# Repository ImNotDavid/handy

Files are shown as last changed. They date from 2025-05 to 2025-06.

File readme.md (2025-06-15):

# HANDY

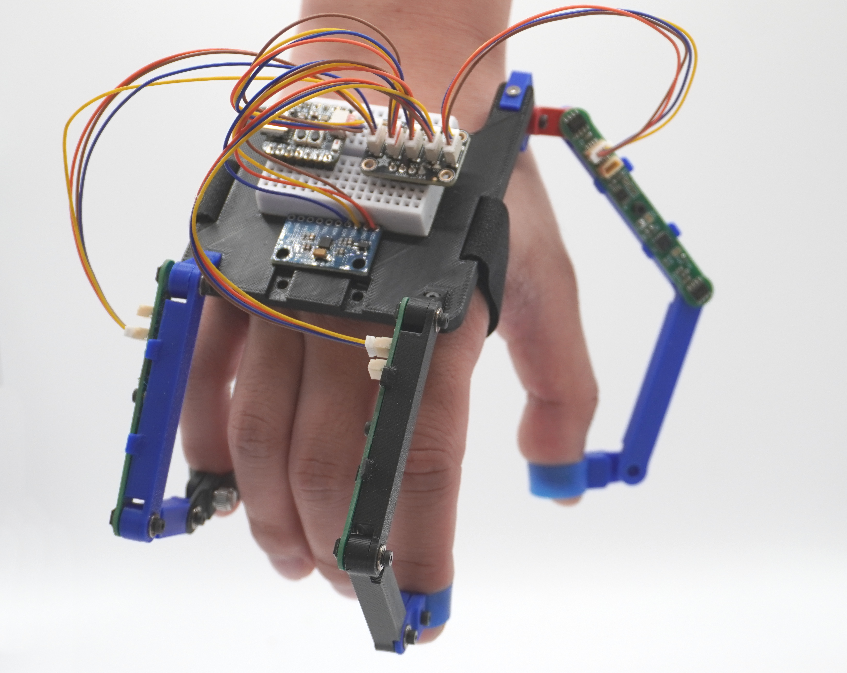
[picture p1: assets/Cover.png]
Handy cover image

## Overview
The Haptically-enabled and Afforable framework to control of Non-anthropomorphic robot manipulators for Data gatheringY (HANDY) is a very affordable data glove and ROS software stack to allow anyone to capture dexterous manipulation data.  

## Hardware 

The 3d model can be found at [this](https://cad.onshape.com/documents/4283529db481f6427532362c/w/a5ad88a1f793d7bc8f76de6a/e/f981b522771d813f689838bc) public onshape project. 

The lenghts of the linkages can be changed by editing variables in the `Passive Link` file or configuration values in `Main Assembly`. The size of the finger mounts can be edited similarly in `Finger Trap Net`. It is highly recommended to use [onshape-to-robot](https://github.com/Rhoban/onshape-to-robot) to convert the assembly into a URDF. The assembly, `URDF` has already been set up for this purpose and the config file [here](handy_ros2\urdf\config.json) has been configured to point to the correct file. You will need to change this to your own URL if you are making modifications. 
All parts can be printed in PLA at 0.16mm layer height. The following off the shelf components are required to assemble the Handy (5 fingered configuration):
- 10 of 6mm x 1mm diametrically magnetised magnet (found [here](https://www.first4magnets.com/product/6mm-dia-x-1mm-thick-diametrically-magnetised-n42-neodymium-magnet-20413)) 
- 20 of M2x3.2x2.5mm heat set insert with OD 
- 20 M2x6mm screws 
- 1 Mini Breadboard
- ESP32-S3 pyqt 

### PCB
All the gerber files for the PCB are found [here](pcb\output\handy_gbr.zip) and can be ordered from a manufacturer like JLCPCB for a low price. The component list is included in the KiCad project. 

# Software

## Firmware

The firmware exists as a platformio project in the [`firmware`](firmware) folder. This can be modified to work on any ESP-32 based microcontroller by selecting the appropriate chip in `platformio.ini`. 

## ROS

The ROS nodes are written for ROS2 Humble. To install, simply clone this repo into your `ros_ws/src/` folder and `colcon build` in your workspace. Note that rosdeps are not properly setup so some work may need to done manually installing required python packages. 

After sourcing the workspace, running `ros2 launch handy handy.launch.py` should deploy the software stack including the kinematic mapping to 2 fingered manipulator. This can be visualised in rviz. 

# Videos
Here are some examples of Handy being used for manipulation tasks:

https://github.com/user-attachments/assets/99e4fd3a-1bce-4f82-9469-66eb39cce375

https://github.com/user-attachments/assets/1d073916-30b5-41df-a31d-748b461f2f68

# Contact
If you have any problems (I suspect you will), feel free to reach out to me through [email](mailto:dc1021@ic.ac.uk) or [discord](https://discord.gg/3YKPjgskS3).

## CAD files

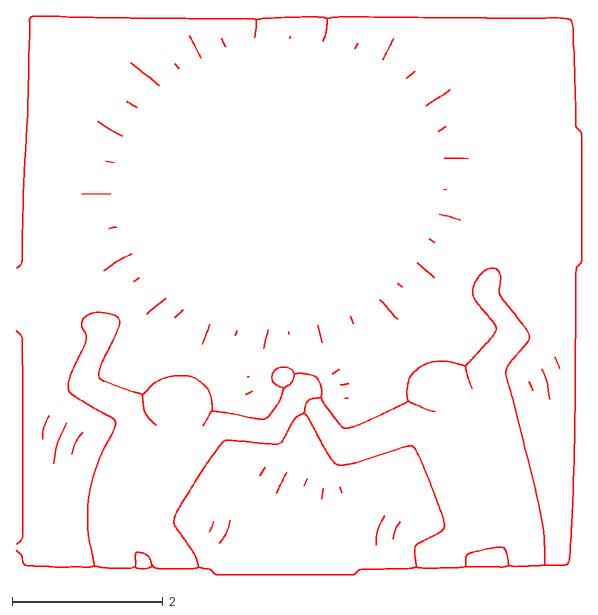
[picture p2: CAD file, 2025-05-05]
pcb/footprints/Haring.dxf
7.52 x 7.42

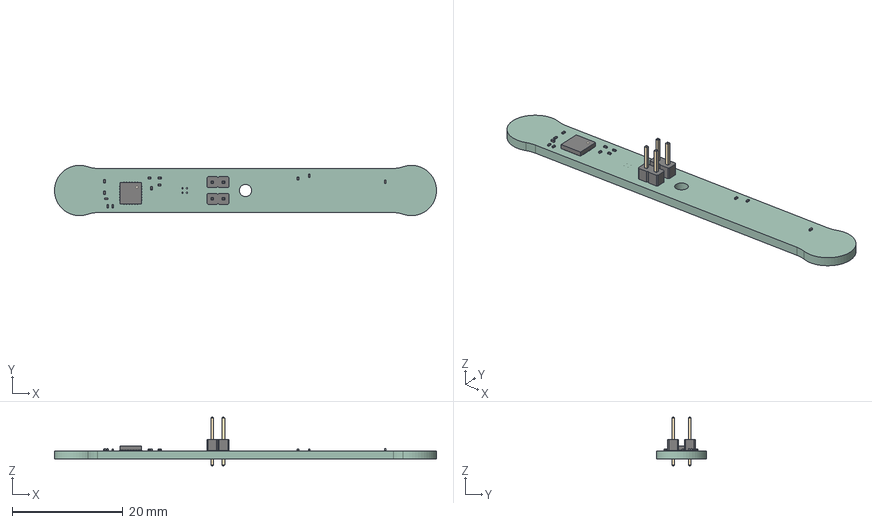
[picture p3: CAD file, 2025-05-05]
pcb/handy.step
69.1 x 9.10 x 8.80 mm
R_0201_0603Metric x 10
C_0201_0603Metric x 2
PinHeader_1x02_P2.00mm_Vertical x 2
Texas_RGE0024C_VQFN-24-1EP_4x4mm_P0.5mm_EP2.1x2.1mm
handy_PCB

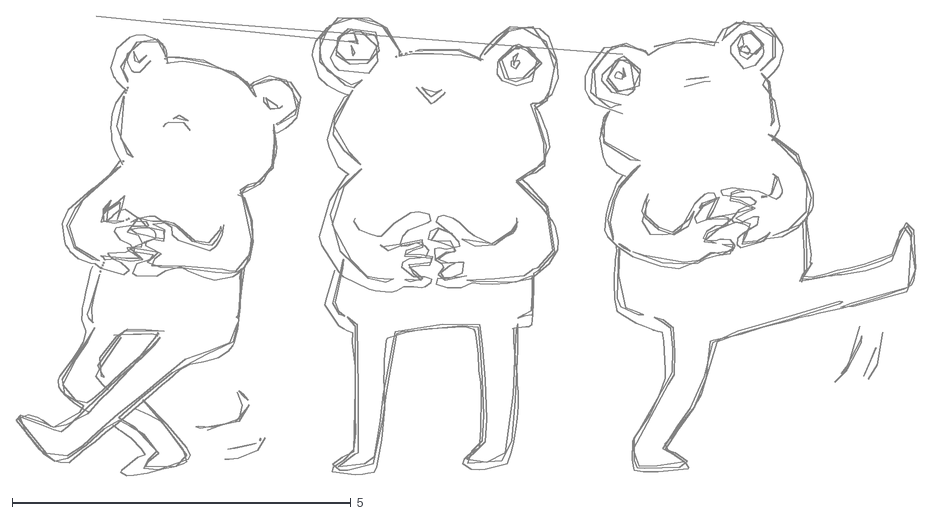
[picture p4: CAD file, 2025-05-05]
pcb/footprints/Froggies.dxf
13.3 x 6.78

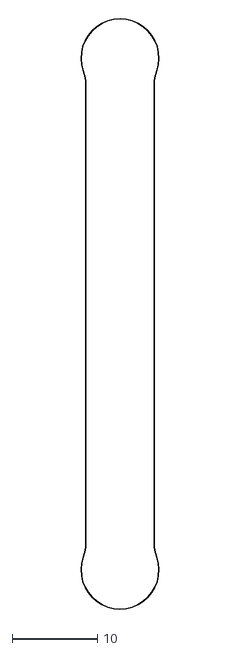
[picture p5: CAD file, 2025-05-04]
pcb/footprints/PCB outline 8mm.dxf
9.91 x 69.7

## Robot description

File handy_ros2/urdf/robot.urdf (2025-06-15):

<?xml version="1.0" ?>
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
<robot name="urdf">
  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
  <link name="base_link">
    <inertial>
      <origin xyz="0 0 0" rpy="0 0 0"/>
      <mass value="1e-09"/>
      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
    </inertial>
  </link>
  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
  <link name="base">
    <inertial>
      <origin xyz="0 0 0" rpy="0 0 0"/>
      <mass value="1e-09"/>
      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
    </inertial>
    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
  </link>
  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
  <link name="encoder_link_assembly__configuration_default">
    <inertial>
      <origin xyz="-0.0339637 -2.62226e-18 0.000778722" rpy="0 0 0"/>
      <mass value="0.000597845"/>
      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
    </inertial>
    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
  </link>
  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
  <link name="passive_link_assembly__configuration_default">
    <inertial>
      <origin xyz="0 0 0" rpy="0 0 0"/>
      <mass value="1e-09"/>
      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
    </inertial>
    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
  </link>
  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
  <link name="part_1">
    <inertial>
      <origin xyz="0 0 0" rpy="0 0 0"/>
      <mass value="1e-09"/>
      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
    </inertial>
    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
  </link>
  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
  <link name="index_tip">
    <origin xyz="0 0 0" rpy="0 -0 0"/>
    <inertial>
      <origin xyz="0 0 0" rpy="0 0 0"/>
      <mass value="1e-9"/>
      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
    </inertial>
  </link>
  <joint name="index_tip_frame" type="fixed">
    <origin xyz="-0.0207217 0.02 7.5e-05" rpy="-1.5708 -0 0"/>
    <parent link="part_1"/>
    <child link="index_tip"/>
    <axis xyz="0 0 0"/>
  </joint>
  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
  <joint name="index_2" type="revolute">
    <origin xyz="-0.045 3.46945e-18 3.46945e-18" rpy="-3.14159 -1.84264e-47 0"/>
    <parent link="passive_link_assembly__configuration_default"/>
    <child link="part_1"/>
    <axis xyz="0 0 1"/>
    <limit effort="10" velocity="10" lower="-3.141592653589793" upper="3.141592653589793"/>
  </joint>
  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
  <joint name="index_1" type="revolute">
    <origin xyz="-0.06 -1.38778e-17 0" rpy="3.14159 1.10559e-47 0"/>
    <parent link="encoder_link_assembly__configuration_default"/>
    <child link="passive_link_assembly__configuration_default"/>
    <axis xyz="0 0 1"/>
    <limit effort="10" velocity="10" lower="-3.141592653589793" upper="3.141592653589793"/>
  </joint>
  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
  <joint name="index_0" type="revolute">
    <origin xyz="0.0259773 -0.0367889 0.0136569" rpy="1.5708 0.785398 1.5708"/>
    <parent link="base"/>
    <child link="encoder_link_assembly__configuration_default"/>
    <axis xyz="0 0 1"/>
    <limit effort="10" velocity="10" lower="-3.141592653589793" upper="3.141592653589793"/>
  </joint>
  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
  <link name="part_2">
    <inertial>
      <origin xyz="0 0 0" rpy="0 0 0"/>
      <mass value="1e-09"/>
      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
    </inertial>
    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
  </link>
  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
  <link name="encoder_link_assembly__configuration_default_2">
    <inertial>
      <origin xyz="0.0260363 8.19879e-20 0.000778722" rpy="0 0 0"/>
      <mass value="0.000597845"/>
      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
    </inertial>
    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
  </link>
  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
  <link name="passive_link_assembly__configuration_thumb">
    <inertial>
      <origin xyz="0 0 0" rpy="0 0 0"/>
      <mass value="1e-09"/>
      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
    </inertial>
    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
  </link>
  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
  <link name="part_1_2">
    <inertial>
      <origin xyz="0 0 0" rpy="0 0 0"/>
      <mass value="1e-09"/>
      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
    </inertial>
    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
  </link>
  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
  <link name="thumb_tip">
    <origin xyz="0 0 0" rpy="0 -0 0"/>
    <inertial>
      <origin xyz="0 0 0" rpy="0 0 0"/>
      <mass value="1e-9"/>
      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
    </inertial>
  </link>
  <joint name="thumb_tip_frame" type="fixed">
    <origin xyz="-0.0207217 -0.02 7.5e-05" rpy="1.5708 -5.55112e-17 3.15544e-30"/>
    <parent link="part_1_2"/>
    <child link="thumb_tip"/>
    <axis xyz="0 0 0"/>
  </joint>
  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
  <joint name="thumb_2" type="revolute">
    <origin xyz="-0.055 -6.93889e-18 -6.07153e-18" rpy="3.14159 -5.55112e-17 3.55596e-14"/>
    <parent link="passive_link_assembly__configuration_thumb"/>
    <child link="part_1_2"/>
    <axis xyz="0 0 1"/>
    <limit effort="10" velocity="10" lower="-3.141592653589793" upper="3.141592653589793"/>
  </joint>
  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
  <joint name="thumb_1" type="revolute">
    <origin xyz="0.06 0 8.67362e-19" rpy="-3.14159 2.22045e-16 3.14159"/>
    <parent link="encoder_link_assembly__configuration_default_2"/>
    <child link="passive_link_assembly__configuration_thumb"/>
    <axis xyz="0 0 1"/>
    <limit effort="10" velocity="10" lower="-3.141592653589793" upper="3.141592653589793"/>
  </joint>
  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
  <joint name="thumb_0" type="revolute">
    <origin xyz="0 0.012 -0.00866025" rpy="3.14159 1.0472 1.5708"/>
    <parent link="part_2"/>
    <child link="encoder_link_assembly__configuration_default_2"/>
    <axis xyz="0 0 1"/>
    <limit effort="10" velocity="10" lower="-3.141592653589793" upper="3.141592653589793"/>
  </joint>
  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
  <joint name="thumb_3" type="revolute">
    <origin xyz="0.0335773 0.0457111 -0.007" rpy="-1.5708 -0 1.5708"/>
    <parent link="base"/>
    <child link="part_2"/>
    <axis xyz="0 0 1"/>
    <limit effort="10" velocity="10" lower="-3.141592653589793" upper="3.141592653589793"/>
  </joint>
  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
  <link name="encoder_link_assembly__configuration_default_3">
    <inertial>
      <origin xyz="-0.0339637 4.49538e-18 0.000927472" rpy="0 0 0"/>
      <mass value="0.000597845"/>
      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
    </inertial>
    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
  </link>
  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
  <link name="passive_link_assembly__configuration_pinky">
    <inertial>
      <origin xyz="0 0 0" rpy="0 0 0"/>
      <mass value="1e-09"/>
      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
    </inertial>
    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
  </link>
  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
  <link name="part_1_3">
    <inertial>
      <origin xyz="0 0 0" rpy="0 0 0"/>
      <mass value="1e-09"/>
      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
    </inertial>
    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
  </link>
  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
  <link name="pinky_tip">
    <origin xyz="0 0 0" rpy="0 -0 0"/>
    <inertial>
      <origin xyz="0 0 0" rpy="0 0 0"/>
      <mass value="1e-9"/>
      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
    </inertial>
  </link>
  <joint name="pinky_tip_frame" type="fixed">
    <origin xyz="-0.0207217 0.02 7.5e-05" rpy="-1.5708 6.16298e-33 0"/>
    <parent link="part_1_3"/>
    <child link="pinky_tip"/>
    <axis xyz="0 0 0"/>
  </joint>
  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
  <joint name="pinky_2" type="revolute">
    <origin xyz="-0.03 3.1225e-17 1.04083e-17" rpy="-5.55112e-17 5.55112e-17 6.66134e-16"/>
    <parent link="passive_link_assembly__configuration_pinky"/>
    <child link="part_1_3"/>
    <axis xyz="0 0 1"/>
    <limit effort="10" velocity="10" lower="-3.141592653589793" upper="3.141592653589793"/>
  </joint>
  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
  <joint name="pinky_1" type="revolute">
    <origin xyz="-0.06 1.04083e-17 4.875e-05" rpy="-3.14159 -5.55112e-17 6.66134e-16"/>
    <parent link="encoder_link_assembly__configuration_default_3"/>
    <child link="passive_link_assembly__configuration_pinky"/>
    <axis xyz="0 0 1"/>
    <limit effort="10" velocity="10" lower="-3.141592653589793" upper="3.141592653589793"/>
  </joint>
  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
  <joint name="pinky_0" type="revolute">
    <origin xyz="-0.0289227 -0.0367889 0.0136569" rpy="-1.5708 0.785398 1.5708"/>
    <parent link="base"/>
    <child link="encoder_link_assembly__configuration_default_3"/>
    <axis xyz="0 0 1"/>
    <limit effort="10" velocity="10" lower="-3.141592653589793" upper="3.141592653589793"/>
  </joint>
  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
  <joint name="base_link_to_base" type="fixed">
    <origin xyz="0 0 0" rpy="0 -0 0"/>
    <parent link="base_link"/>
    <child link="base"/>
    <axis xyz="0 0 1"/>
    <limit effort="10" velocity="10"/>
  </joint>
</robot>

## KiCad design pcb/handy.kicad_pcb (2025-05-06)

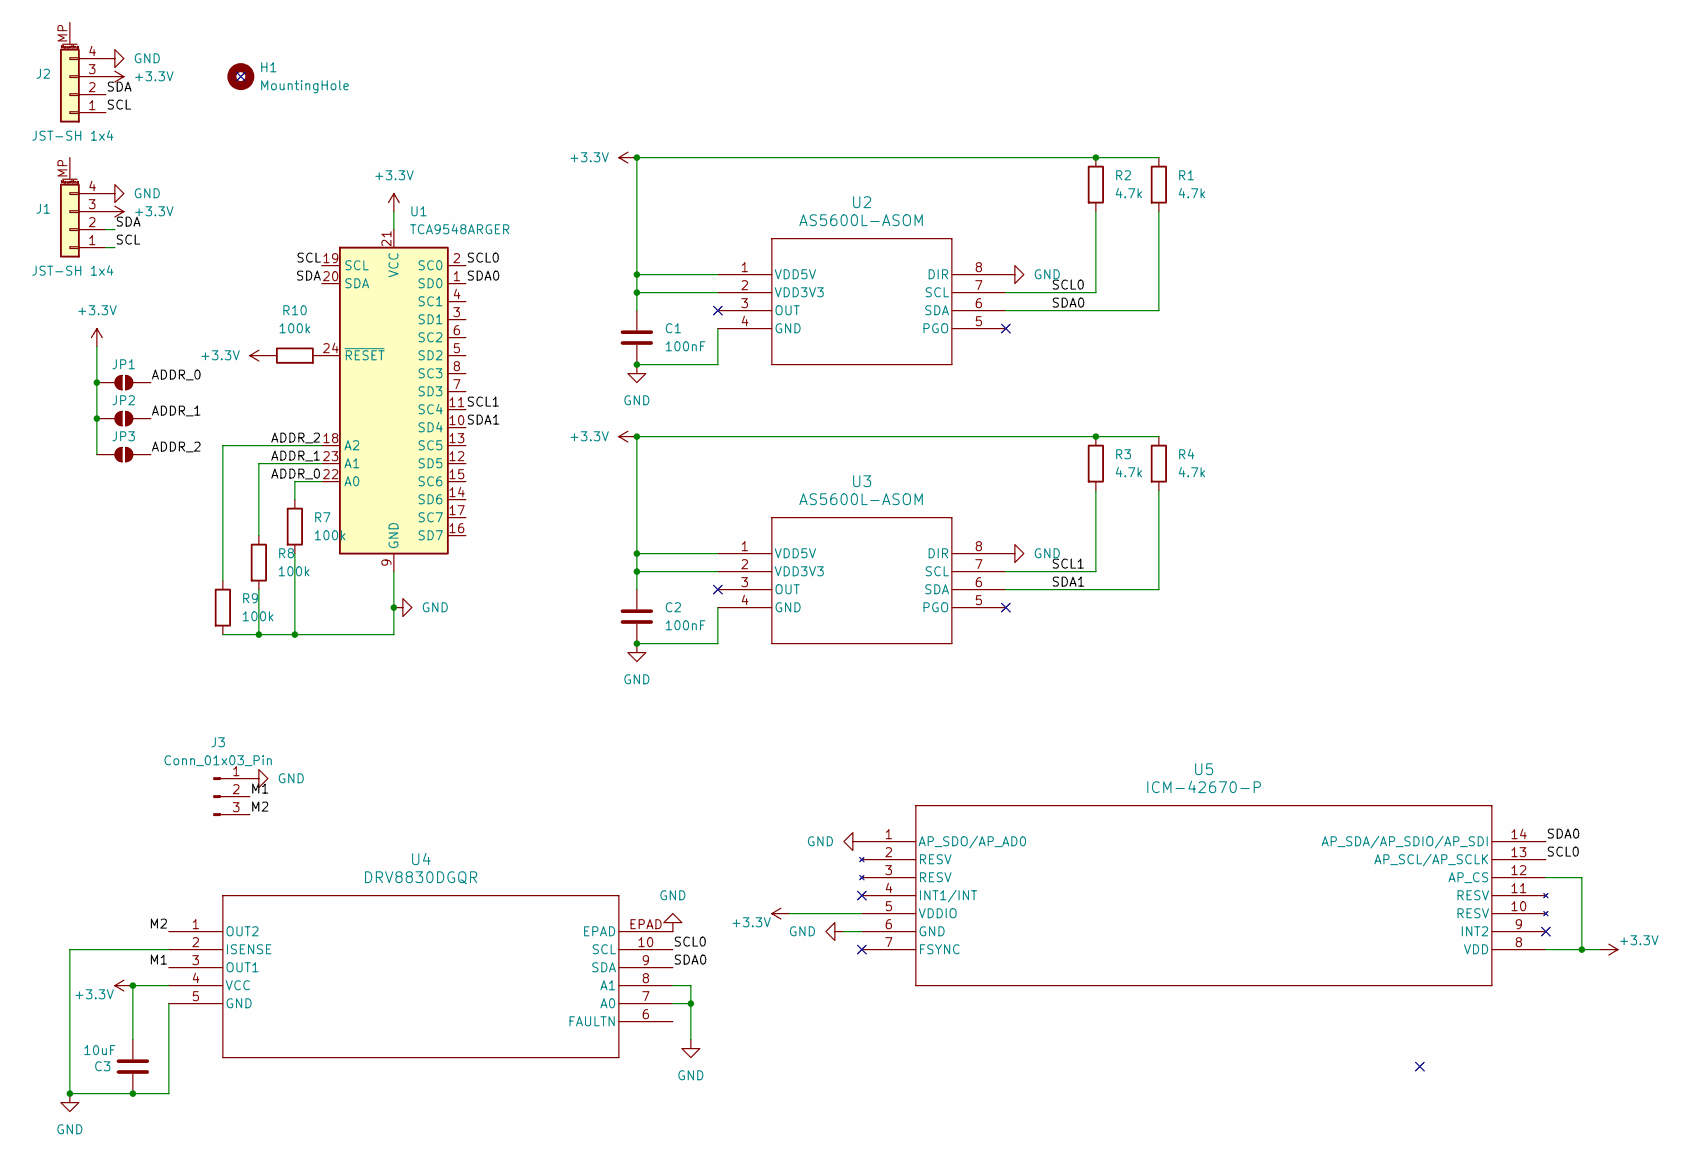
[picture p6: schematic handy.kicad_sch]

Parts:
C1, C2: 100nF; C_0603_1608Metric
C3: 10uF; C_0603_1608Metric
H1: MountingHole; MountingHole_2.2mm_M2_ISO14580_Pad
J1, J2: JST-SH 1x4; JST_SH_BM04B-SRSS-TB_1x04-1MP_P1.00mm_Vertical
J3: Conn_01x03_Pin; PinSocket_1x03_P2.00mm_Vertical
JP1, JP2, JP3: SolderJumper-2_P1.3mm_Open_TrianglePad1.0x1.5mm
R1, R2, R3, R4: 4.7k; R_0603_1608Metric
R7, R8, R9, R10: 100k; R_0603_1608Metric
U1: TCA9548ARGER; Texas_RGE0024C_VQFN-24-1EP_4x4mm_P0.5mm_EP2.1x2.1mm
U2, U3: AS5600L-ASOM; AS5600L-ASOM_AMS
U4: DRV8830DGQR; DGQ10_2P18X1P72
U5: ICM-42670-P; LGA14_2.5X3X0.76_IVS

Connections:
+3.3V: C1.1, C2.1, C3.2, J1.3, J2.3, JP1.2 (B), JP2.1 (A), JP3.1 (A), R1.1, R2.1, R3.1, R4.1, R10.1, U1.21 (VCC), U2.1 (VDD5V), U2.2 (VDD3V3), U3.1 (VDD5V), U3.2 (VDD3V3), U4.4 (VCC), U5.5 (VDDIO), U5.8 (VDD), U5.12 (AP_CS)
/ADDR_0: JP1.1 (A), R7.1, U1.22 (A0)
/ADDR_1: JP2.2 (B), R8.1, U1.23 (A1)
/ADDR_2: JP3.2 (B), R9.1, U1.18 (A2)
/M1: J3.2, U4.3 (OUT1)
/M2: J3.3, U4.1 (OUT2)
/SCL: J1.1, J2.1, U1.19 (SCL)
/SCL0: R2.2, U1.2 (SC0), U2.7 (SCL), U4.10 (SCL), U5.13 (AP_SCL/AP_SCLK)
/SCL1: R3.2, U1.11 (SC4), U3.7 (SCL)
/SDA: J1.2, J2.2, U1.20 (SDA)
/SDA0: R1.2, U1.1 (SD0), U2.6 (SDA), U4.9 (SDA), U5.14 (AP_SDA/AP_SDIO/AP_SDI)
/SDA1: R4.2, U1.10 (SD4), U3.6 (SDA)
GND: C1.2, C2.2, C3.1, J1.4, J2.4, J3.1, R7.2, R8.2, R9.2, U1.9 (GND), U2.4 (GND), U2.8 (DIR), U3.4 (GND), U3.8 (DIR), U4.2 (ISENSE), U4.5 (GND), U4.7 (A0), U4.8 (A1), U4.EPAD, U5.1 (AP_SDO/AP_AD0), U5.6 (GND)
unnamed: R10.2, U1.24 (~RESET)

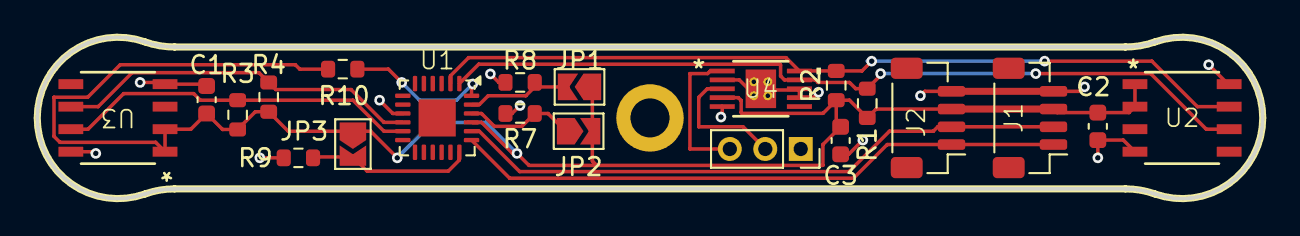
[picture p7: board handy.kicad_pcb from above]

Board: 2 copper layers, 69.1 x 9.1 mm, 22 parts (0 on the bottom side), 14 nets.

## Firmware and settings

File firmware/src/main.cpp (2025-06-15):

#include "finger.h"
#include "config.h"
#include "imu.h"
#include <Adafruit_NeoPixel.h>

#define FAULTn  16
float config_list[][4] = FINGER_CONFIG;
const int fingersNo = sizeof(config_list) / sizeof(config_list[0]);
Finger fingers[fingersNo];
int delay_micros = 1000000 / FREQ;
int prev_micros = micros();
Adafruit_NeoPixel led(LED_COUNT, LED_PIN, NEO_GRBW + NEO_KHZ800);

int target_finger,haptic_value;
#define BUFFER_SIZE 32
char inputBuffer[BUFFER_SIZE];
uint8_t bufferIndex = 0;
bool receiving = false;

void parseInput(const char* data) {
  // Expect format: "12,34"
  char* comma = strchr(data, ',');
  if (comma != NULL) {
    *comma = '\0';  // Split the string at the comma
    target_finger = atoi(data);
    haptic_value = atoi(comma + 1);

    //Serial.print("Parsed: ");
    //Serial.print(target_finger);
    //Serial.print(" and ");
    //Serial.println(haptic_value);
    fingers[target_finger].setFeedback(static_cast<uint8_t>(haptic_value));
  } else {
    Serial.println("Error: no comma found.");
  }
}


void setup()
{
  pinMode(LED_ENABLE,OUTPUT);
  digitalWrite(LED_ENABLE,HIGH);
  led.begin();           // INITIALIZE NeoPixel strip object (REQUIRED)
  led.setBrightness(BRIGHTNESS);
  led.setPixelColor(0, led.Color(194, 24, 7));
  led.show();            


  
  Wire.begin(SDA1, SCL1);
  Serial.begin(115200);
  Serial.println("\nHandy Test");
  setupIMU();

  // Setup fingers
  for (int i = 0; i < fingersNo; i++)
  {
    fingers[i] = Finger(static_cast<int>(config_list[i][0]),config_list[i][1],config_list[i][2],static_cast<bool>(config_list[i][3]));
  }

  for (int i = 0; i < fingersNo; i++)
  {
    fingers[i].initHaptics();
  }

  fingers[2].haptic_motor.setSpeed(0);
  led.setPixelColor(0, led.Color(147, 112, 219));
  led.show();    
}

void loop()
{
  int current = micros();
  if (current > (prev_micros + delay_micros))
  {
    getOrientation();
    float angles[10] = { fingers[0].readAngle(0), fingers[0].readAngle(1), fingers[0].readAngle(2), 
                        0.0, fingers[1].readAngle(0), fingers[1].readAngle(1), fingers[1].readAngle(2), 
                        fingers[2].readAngle(0), fingers[2].readAngle(1), fingers[2].readAngle(2)};
    Serial.write(0xAA);
    for(int i = 0; i < 10; i++){
      byte* outBytes = (byte*) &angles[i];
      Serial.write(outBytes,sizeof(float));
    }
    float outValue = filter.getRoll(); 
    Serial.write((byte*)&outValue,sizeof(float));
    outValue = filter.getPitch(); 
    Serial.write((byte*)&outValue,sizeof(float));
    outValue = filter.getYaw(); 
    Serial.write((byte*)&outValue,sizeof(float));
    Serial.write(0x55);
    prev_micros = micros();
  }
  while (Serial.available()) {
    char inChar = (char)Serial.read();

    if (inChar == '<') {
      receiving = true;
      bufferIndex = 0;
    } else if (inChar == '>') {
      receiving = false;
      inputBuffer[bufferIndex] = '\0';  // Null-terminate the string
      parseInput(inputBuffer);
    } else if (receiving && bufferIndex < BUFFER_SIZE - 1) {
      inputBuffer[bufferIndex++] = inChar;
    }
  }
}

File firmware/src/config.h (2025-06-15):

#define THUMB 
#define INDEX
// #define MIDDLE
// #define RING
#define PINKY

#define FREQ 100
#define IMU 


#ifdef THUMB
#define THUMB_ADDR {0x72,
#define THUMB_OFFSETS -135.25, -297.42,
#define THUMB_HAPTIC 0.0},
#else
#define THUMB_ADDR 
#define THUMB_OFFSETS
#define THUMB_HAPTIC 
#endif

#ifdef INDEX
#define INDEX_ADDR {0x70,
#define INDEX_OFFSETS -122.34, -159.91,
#define INDEX_HAPTIC 0.0},
#else
#define INDEX_ADDR 
#define INDEX_OFFSETS
#define INDEX_HAPTIC 
#endif

#ifdef MIDDLE
#define MIDDLE_ADDR {0x72,
#define MIDDLE_OFFSETS 0.0, 0.0,
#define MIDDLE_HAPTIC 0.0},
#else
#define MIDDLE_ADDR 
#define MIDDLE_OFFSETS
#define MIDDLE_HAPTIC 
#endif

#ifdef RING
#define RING_ADDR {0x72,
#define RING_OFFSETS 0.0, 0.0,
#define RING_HAPTIC 0.0},
#else
#define RING_ADDR 
#define RING_OFFSETS
#define RING_HAPTIC 
#endif

#ifdef PINKY
#define PINKY_ADDR {0x73,
#define PINKY_OFFSETS 210.5, -300.0,
#define PINKY_HAPTIC 1.0},
#else
#define PINKY_ADDR 
#define PINKY_OFFSETS
#define PINKY_HAPTIC 
#endif

#define FINGER_CONFIG   {\
                    THUMB_ADDR THUMB_OFFSETS THUMB_HAPTIC  \
                    INDEX_ADDR INDEX_OFFSETS INDEX_HAPTIC  \
                    MIDDLE_ADDR MIDDLE_OFFSETS MIDDLE_HAPTIC \
                    RING_ADDR RING_OFFSETS RING_HAPTIC   \
                    PINKY_ADDR PINKY_OFFSETS PINKY_HAPTIC  \
                    }


#define LED_COUNT 1
#define LED_PIN 39
#define LED_ENABLE 38
#define BRIGHTNESS 25

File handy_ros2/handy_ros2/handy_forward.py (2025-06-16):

import rclpy
import numpy as np
from rclpy.node import Node
from tf2_ros import Buffer, TransformListener, TransformBroadcaster
from geometry_msgs.msg import Vector3, TransformStamped
from handy_ros2.utils import quaternion_from_euler
from std_msgs.msg import Int16MultiArray

def calculateRotation(vector0: np.array, vector1: np.array):
    n = np.cross(vector0, vector1)
    if np.allclose(n, 0):
        return np.identity(3)

    u = n / np.linalg.norm(n)
    v = np.array([1.0, 0.0, 0.0])
    
    if np.allclose(u, v):
        return np.identity(3)
    elif np.allclose(u, -v):
        return np.array([
            [1, 0,  0],
            [0, -1, 0],
            [0, 0, -1]
        ])
    
    k = np.cross(u, v)
    c = np.dot(u, v)
    s = np.linalg.norm(k)

    kx, ky, kz = k
    k_skew = np.array([
        [0, -kz, ky],
        [kz, 0, -kx],
        [-ky, kx, 0]
    ])

    k_skew_squared = k_skew @ k_skew
    r = np.identity(3) + k_skew + k_skew_squared * ((1 - c) / (s ** 2))
    phi = np.deg2rad(-5)
    A = np.array([
        [1, 0,  0],
        [0, np.cos(phi),  -np.sin(phi)],
        [0, np.sin(phi),  np.cos(phi)]
    ])
    r = A@r
    return r




def vec3ToNp(vector:Vector3)->np.array:
    x = vector.x
    y = vector.y
    z = vector.z
    return np.array([x,y,z])


class FrameListener(Node):
    def __init__(self):
        super().__init__('handy_forward')
        self.tf_buffer = Buffer()
        self.tf_listener = TransformListener(self.tf_buffer, self)
        self.tf_publisher = TransformBroadcaster(self)
        self.timer = self.create_timer(0.01, self.get_transform)

    def publish_transform(self, vector_i:np.array, vector_t:np.array):
        r = calculateRotation(vector_i,vector_t)
        vector_i = np.matmul(r,np.transpose(vector_i))
        vector_t = np.matmul(r,np.transpose(vector_t))


        q = quaternion_from_euler(0,0,0)
        t = TransformStamped()
        t.header.stamp = self.get_clock().now().to_msg()
        t.header.frame_id = 'base'
        t.child_frame_id = 'virtual_base'
        t.transform.rotation.x = q[0]
        t.transform.rotation.y = q[1]
        t.transform.rotation.z = q[2]
        t.transform.rotation.w = q[3]
        self.tf_publisher.sendTransform(t)

        t = TransformStamped()
        t.header.stamp = self.get_clock().now().to_msg()
        t.header.frame_id = 'virtual_base'
        t.child_frame_id = 'virtual_index'
        t.transform.translation.x = vector_i[0]
        t.transform.translation.y = vector_i[1]
        t.transform.translation.z = -vector_i[2]
        self.tf_publisher.sendTransform(t)
        t = TransformStamped()

        t.header.stamp = self.get_clock().now().to_msg()
        t.header.frame_id = 'virtual_base'
        t.child_frame_id = 'virtual_thumb'
        t.transform.translation.x = vector_t[0]
        t.transform.translation.y = vector_t[1]
        t.transform.translation.z = -vector_t[2]
        self.tf_publisher.sendTransform(t)

    def get_transform(self):
        try:
            base_to_index_tip = self.tf_buffer.lookup_transform(
                'base',  # target_frame
                'index_tip',  # source_frame
                rclpy.time.Time()) 
            
            base_to_index_base = self.tf_buffer.lookup_transform(
                'base',  # target_frame
                'encoder_link_assembly__configuration_default',  # source_frame
                rclpy.time.Time())
            
            base_to_thumb = self.tf_buffer.lookup_transform(
                'base',
                'thumb_tip',
                rclpy.time.Time()
            )

            base_to_thumb_base = self.tf_buffer.lookup_transform(
                'base',
                'part_2',
                rclpy.time.Time()
            )


            
            o_to_f = vec3ToNp(base_to_index_tip.transform.translation)
            o_to_bf = vec3ToNp(base_to_index_base.transform.translation)
            b_to_f = o_to_f-o_to_bf
            o_to_t = vec3ToNp(base_to_thumb.transform.translation)
            bf_to_bt = -o_to_bf + o_to_t
            self.publish_transform(b_to_f,bf_to_bt)
            
        except Exception as e:
            self.get_logger().warn(f'Could not transform: {e}')
            pass

    
def main():
    rclpy.init()
    node = FrameListener()
    rclpy.spin(node)
    rclpy.shutdown()

if __name__ == '__main__':
    main()

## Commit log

2025-05-04 added as5600 footprint
    [handy.kicad_sch]
2025-05-04 encoders and outline
    [PCB outline 8mm.dxf, handy.kicad_pcb, handy.kicad_sch]
2025-05-05 first draft
    [handy.kicad_pcb, handy.kicad_sch, handy.step]
2025-05-05 fuck my chungus life
    [handy.kicad_pcb, handy.kicad_sch]
2025-05-05 routed without imu
    [handy.kicad_pcb, handy.kicad_sch]
2025-05-05 added missing pullup and capacitor
    [handy.kicad_pcb, handy.kicad_sch]
2025-05-05 added graphics
    [Froggies.dxf, Haring.dxf, handy.kicad_pcb]
2025-05-06 Add gbr files and fixed silkscreen
    [handy-B_Cu.gbr, handy-B_Mask.gbr, handy-B_Paste.gbr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]
2025-05-06 Changed via spacing
    [handy-B_Cu.gbr, handy-B_Mask.gbr, handy-B_Paste.gbr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]
2025-05-13 fixed resistor values
    [handy.kicad_sch]
2025-05-15 reformat project
    [Froggies.dxf, Haring.dxf, PCB outline 8mm.dxf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]
2025-05-19 multiple fingers with offset
2025-05-19 ros2 basic package
    [robot.urdf]
2025-05-19 joint bridge base code
2025-05-20 handy bridge complete
    [robot.urdf]
2025-05-21 imu integration
2025-06-01 increased polling rate, added imu
2025-06-02 adjusted for 3 fingers
2025-06-15 figure graphing
    [handy.kicad_sch]
2025-06-15 added pinky
    [robot.urdf]
